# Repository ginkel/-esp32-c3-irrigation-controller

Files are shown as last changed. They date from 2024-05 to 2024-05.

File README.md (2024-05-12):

# ESP32-C3 Plant Watering Controller

A custom PCB for an ESP32-C3 based plant watering controller that features two channels to drive 12V water pumps and one input to check for low water level. If using esphome as [firmware](#firmware) it can be easily integrated into [Home Assistant](https://www.home-assistant.io/).

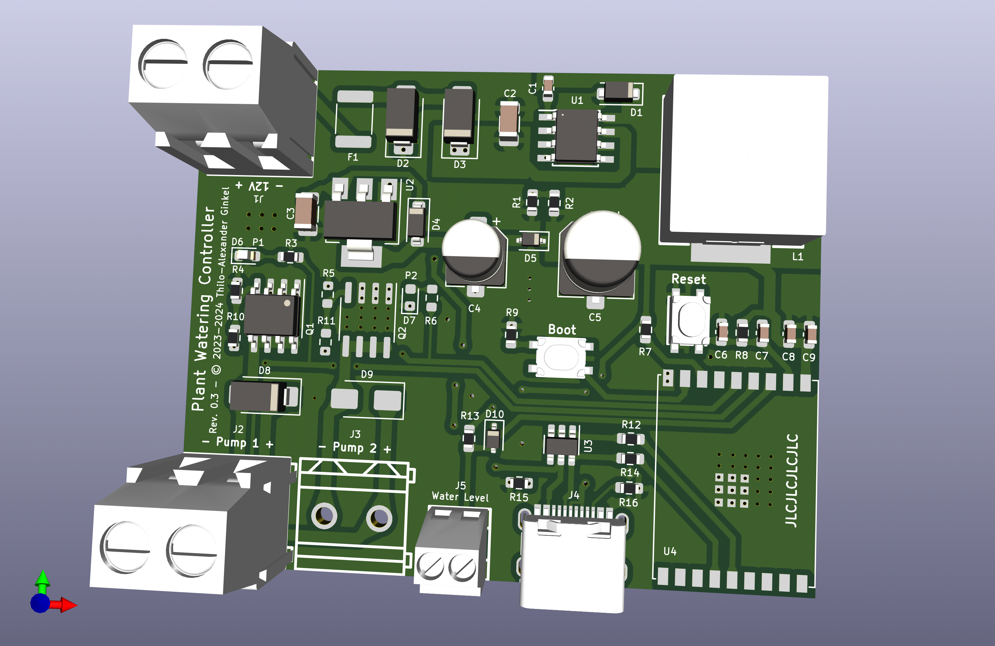
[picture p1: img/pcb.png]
PCB rendering


If you'd like to solder the PCB yourself, the smallest component to be soldered is 0603. The list of components and their placement is available as [interactive BOM](bom/ibom.html).

If you only need one channel (for a single pump), you can leave R5, R6, R11 D7, D9, Q2 and J3 unpopulated.

Documentation is probably far from complete. If you are missing a piece of the puzzle, feel free to open an issue or improve the documentation using a PR.

## Schematic

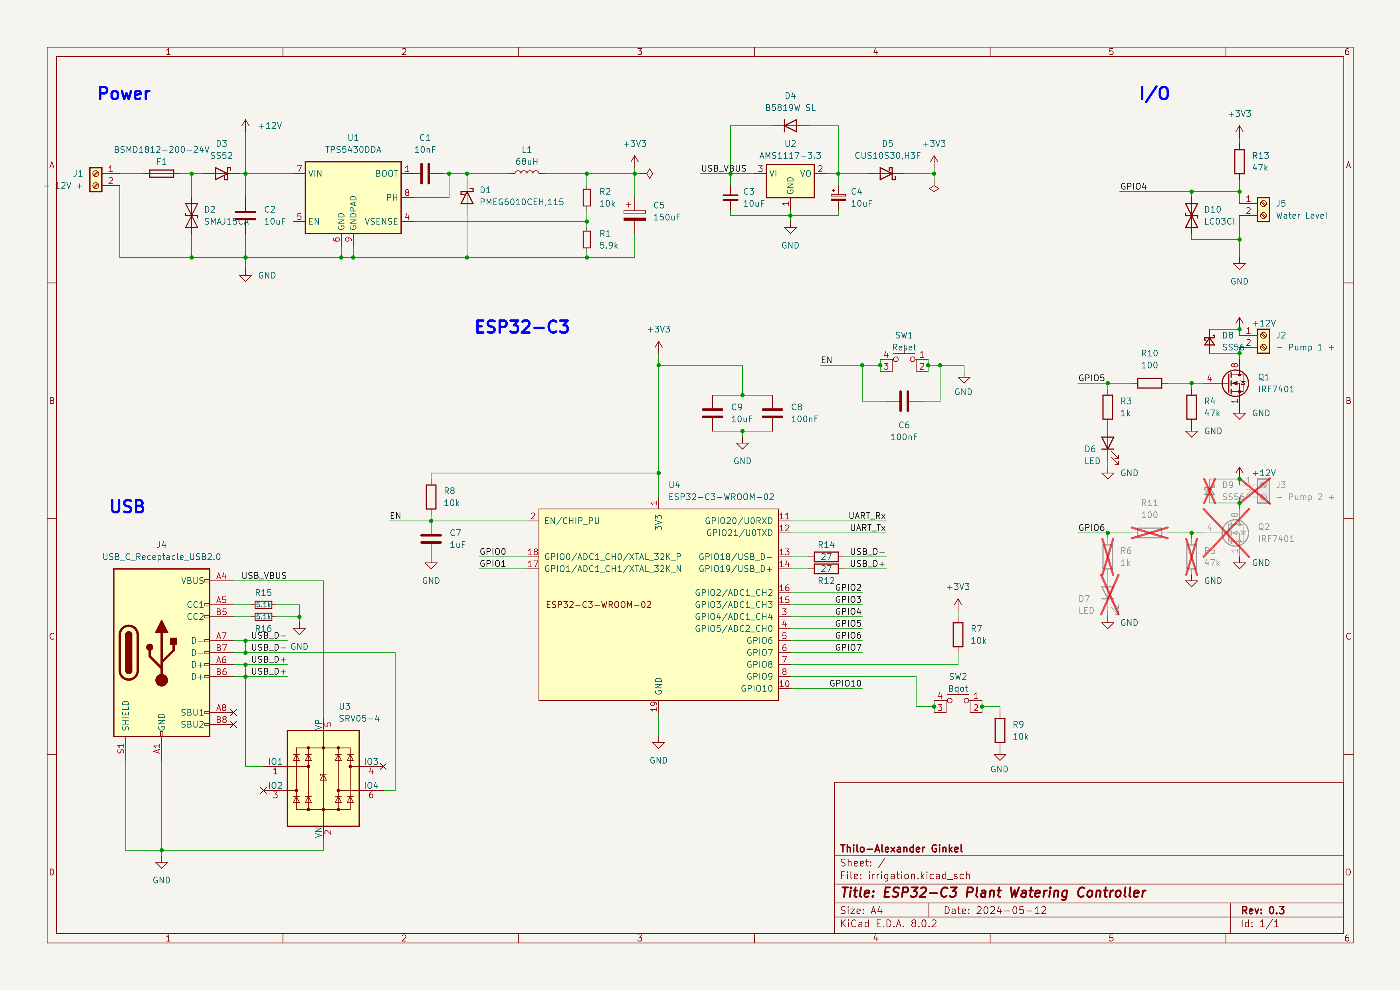
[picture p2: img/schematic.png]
schematics


## BOM

| References | Value | LCSC part # |
|---|---|---|
| C1 | 10nF | C57112 |
| C2 | 10uF | C15849 |
| C3 | 10uF | C89632 |
| C4 | 10uF | C336204 |
| C5 | 150uF | C242120 |
| C6, C8 | 100nF | C1591 |
| C7 | 1uF | C15849 |
| C9 | 10uF | C194427 |
| R2, R7, R8, R9 | 10k | C25804 |
| R3, R6 | 1k | C21190 |
| R4, R5, R13 | 47k | C25819 |
| R10, R11 | 100 | C22775 |
| R12, R14 | 27 | C863706 |
| R15, R16 | 5.1k | C23186 |
| R1 | 5.9k | C23071 |
| L1 | 68uH | C694542 |
| D1 | PMEG6010CEH,115 | C110797 |
| D2 | SMAJ15CA | C110044 |
| D3 | SS52 | C727051 |
| D4 | B5819W SL | C8598 |
| D5 | CUS10S30,H3F | C146335 |
| D6, D7 | LED | C434419 |
| D8, D9 | SS56 | C2904059 |
| D10 | LC03CI | C384865 |
| U1 | TPS5430DDA | C9864 |
| U2 | AMS1117-3.3 | C347222 |
| U3 | SRV05-4 | C85364 |
| U4 | ESP32-C3-WROOM-02 | C2934560 |
| F1 | BSMD1812-200-24V | C206993 |
| SW1, SW2 | XUNPU TS-1089S-02526 | C455282 |
| Q1, Q2 | IRF7401 | C5346818 |
| J1, J2, J3 | DB128L-5.08-2P-GN-P  | C430600 |
| J4 | USB-C Connector | C165948 |
| J5 | DB125-2.54-2P-GN-S | C918120 |

I am sourcing my components from LCSC. If you also do, the LCSC part # may be helpful.

## External Parts

For a full-fledged plant watering solution you'll need some additional components/parts. Links go to AliExpress, but you can of course source the components from other sources if you prefer a different suppliers.

* [Submersible 12V water pump](https://aliexpress.com/item/1005005489175847.html)
* [Water level sensor](https://aliexpress.com/item/1005004306055007.html)
* [Water filter (8mm)](https://aliexpress.com/item/1005005032983727.html)
* [Sprinklers](https://aliexpress.com/item/1005004917374250.html)
* [8mm to 4mm connector](https://aliexpress.com/item/1005004875653640.html)
* 8mm hose
* 4mm hose
* Water reservoir, e.g., IKEA HÅLLBAR (35 l)

## Firmware

The firmware I am running on the controller is based on [esphome](https://esphome.io/). I am using the following snippet (for a single channel and a moisture sensor named `sensor.plant_herbs_balcony_soil_moisture`), which you'll probably want to customize to integrate with your Home Assistant instance and WiFi.

```
globals:
  - id: last_run
    type: time_t
    restore_value: yes
    initial_value: '0'

esphome:
  name: plant-watering
  name_add_mac_suffix: true
  friendly_name: ESP32-C3 Plant Watering Controller
  platformio_options:
    board_build.flash_mode: dio
    board_build.f_flash: 40000000L
    board_build.flash_size: 4MB
    # run with 80 MHz
    board_build.f_cpu: 80000000L

esp32:
  board: esp32-c3-devkitm-1
  framework:
    type: esp-idf
    sdkconfig_options:
      CONFIG_COMPILER_OPTIMIZATION_SIZE: y
  variant: esp32c3

mqtt:
  broker: [...]
  username: [...]
  password: [...]
  on_message:
    - topic: esphome/plant_watering/pump1
      payload: 'ON'
      then:
        - if:
            condition:
              binary_sensor.is_on: water_level
            then:
              - globals.set:
                  id: last_run
                  value: !lambda 'return id(homeassistant_time).now().timestamp;'
              - logger.log: "Turning irrigation 'pump1' on"
              - output.turn_on: pump1
              - logger.log: "Waiting 20s"
              - delay: 20s
              - logger.log: "Turning irrigation 'pump1' off"
              - output.turn_off: pump1
            else:
              - logger.log: "Water level is critical - refusing to turn on irrigation"

output:
  - platform: gpio
    pin:
      number: GPIO5
      mode:
        output: true
        pulldown: true
      drive_strength: 5mA
    id: pump1
  - platform: gpio
    pin:
      number: GPIO6
      mode:
        output: true
        pulldown: true
      drive_strength: 5mA
    id: pump2

binary_sensor:
  - platform: gpio
    pin:
      number: GPIO4
      mode:
        input: true
      inverted: false
    name: "Water Level"
    id: water_level
    filters:
      - delayed_on: 1s
      - delayed_off: 1s
    on_release:
      then:
        - logger.log: "Water level critical - turning off all pumps"
        - output.turn_off: pump1
        - output.turn_off: pump2

sensor:
  - platform: uptime
    name: "ESP32-C3 Plant Watering Controller Uptime"

  - platform: wifi_signal
    name: "ESP32-C3 Plant Watering Controller WiFi Signal"
    update_interval: 15s

  - platform: homeassistant
    name: "Soil humidity"
    entity_id: sensor.plant_herbs_balcony_soil_moisture
    id: plant_herbs_balcony_soil_moisture

text_sensor:
  - platform: template
    name: "ESP32-C3 Plant Watering Controller Last Run"
    icon: mdi:clock-start
    lambda: |-
      return ESPTime::from_epoch_local(id(last_run)).strftime("%Y-%m-%dT%H:%M:%S");
    update_interval: 60s

time:
  - platform: homeassistant
    id: homeassistant_time
    on_time:
      - cron: '00 /5 18-6 * * *'
        then:
        - if:
            condition:
              and:
                - binary_sensor.is_on: water_level
                - lambda: |-
                    return id(plant_herbs_balcony_soil_moisture).state < 55;
                - lambda: |-
                    return id(homeassistant_time).now().is_valid() && (id(homeassistant_time).now().timestamp - id(last_run) > 43200);
            then:
              - globals.set:
                  id: last_run
                  value: !lambda 'return id(homeassistant_time).now().timestamp;'
              - logger.log: "Turning irrigation 'pump1' on"
              - output.turn_on: pump1
              - logger.log: "Waiting 20s"
              - delay: 20s
              - logger.log: "Turning irrigation 'pump1' off"
              - output.turn_off: pump1
            else:
              - logger.log:
                  format: "Water level: %d, average soil moisture: %.1f - refusing to water plants"
                  args: ['id(water_level).state', 'id(weighted_soil_moisture).state']
```

## Integration

The PCB does not offer a built-in mechanism to measure soil humidity, but the [b-parasite](https://github.com/rbaron/b-parasite) open source project provides a suitable DIY capacitive soil moisture sensor that can easily be integrated using ZigBee / Home Assistant.

## Action Shots

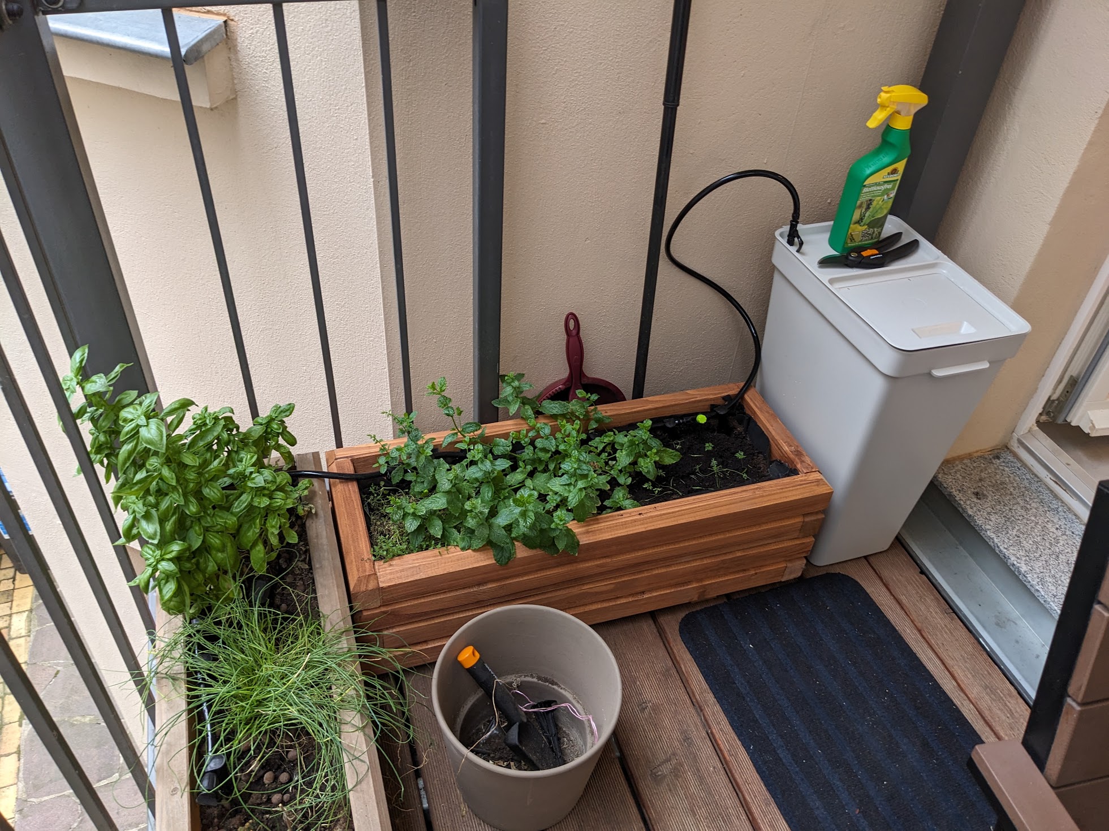
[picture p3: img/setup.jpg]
setup


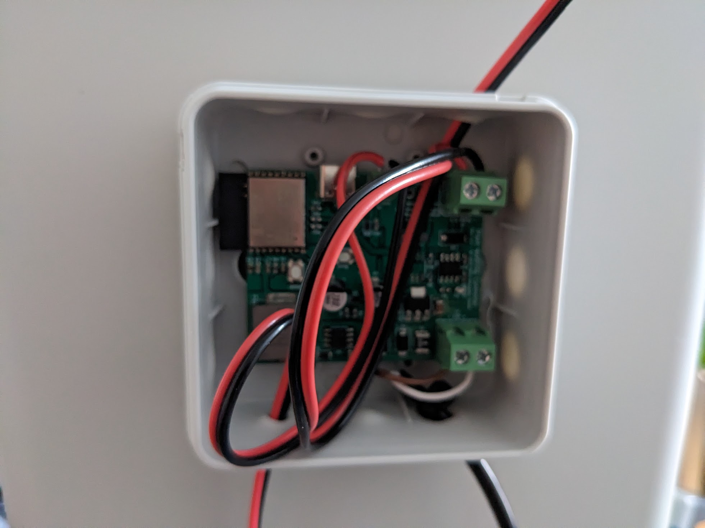
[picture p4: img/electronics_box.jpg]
electronics


## License
The hardware and associated design files are released under the [Creative Commons CC BY-SA 4.0 license](https://creativecommons.org/licenses/by-sa/4.0/).

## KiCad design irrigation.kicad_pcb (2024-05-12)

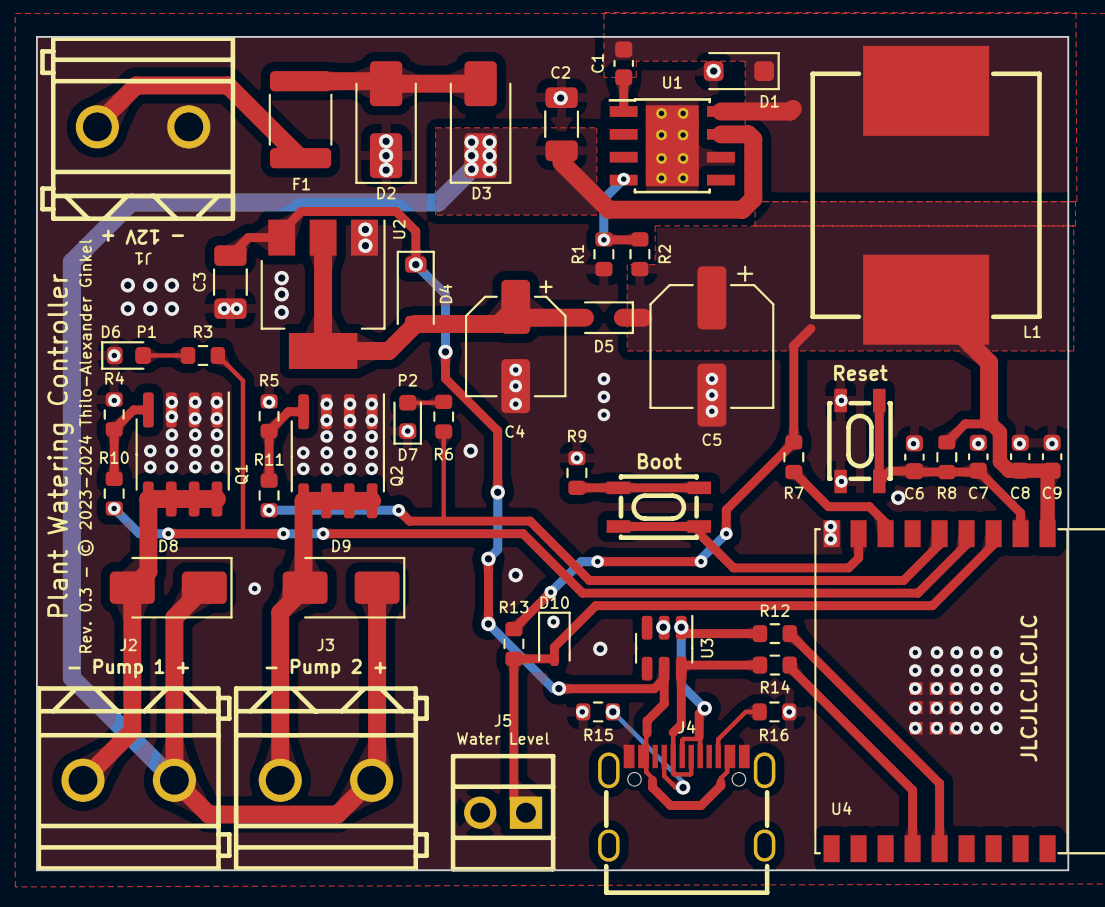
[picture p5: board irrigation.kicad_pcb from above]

Board: 2 copper layers, 57.3 x 46.3 mm, 50 parts (0 on the bottom side), 29 nets.

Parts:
C1: 10nF; C_0603_1608Metric
C2, C3: 10uF; C_1206_3216Metric
C4: 10uF; CP_Elec_5x5.8
C5: 150uF; CP_Elec_6.3x7.7
C6, C8: 100nF; C_0603_1608Metric
C7: 1uF; C_0603_1608Metric
C9: 10uF; C_0603_1608Metric
D1: PMEG6010CEH,115; D_SOD-123F
D2: SMAJ15CA; D_SMA
D3: SS52; D_SMA
D4: B5819W SL; D_SOD-123
D5: CUS10S30,H3F; D_SOD-323
D6, D7: LED; LED_0603_1608Metric
D8, D9: SS56; D_SMA
D10: LC03CI; D_SOD-323
F1: BSMD1812-200-24V; Fuse_1812_4532Metric
J1: - 12V +; CONN-TH_2P-P5.08_DB128L-5.08-2P-GN-P
J2: - Pump 1 +; CONN-TH_2P-P5.08_DB128L-5.08-2P-GN-P
J3: - Pump 2 +; CONN-TH_2P-P5.08_DB128L-5.08-2P-GN-P
J4: USB_C_Receptacle_USB2.0; USB-C_SMD-TYPE-C-31-M-12
J5: Water Level; CONN-TH_DB125-2.54-2P-GN
L1: 68uH; IND-SMD_L12.6-W13.5
Q1, Q2: IRF7401; SOIC-8_3.9x4.9mm_P1.27mm
R1: 5.9k; R_0603_1608Metric
R2, R7, R8, R9: 10k; R_0603_1608Metric
R3, R6: 1k; R_0603_1608Metric
R4, R5, R13: 47k; R_0603_1608Metric
R10, R11: 100; R_0603_1608Metric
R12, R14: 27; R_0603_1608Metric
R15, R16: 5.1k; R_0603_1608Metric
SW1: Reset; SW-SMD_4P-L4.2-W3.3-P2.15-LS5.1
SW2: Boot; SW-SMD_4P-L4.2-W3.3-P2.15-LS5.1
U1: TPS5430DDA; TI_SO-PowerPAD-8_ThermalVias
U2: AMS1117-3.3; SOT-223-3_TabPin2
U3: SRV05-4; SOT-23-6
U4: ESP32-C3-WROOM-02

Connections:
+3V3: C5.1, C8.1, C9.1, D5.1 (K), L1.2, R2.1, R7.1, R8.1, R13.2, U4.1 (3V3)
+12V: C2.1, D3.1 (K), D8.1 (K), D9.1 (K), J2.1, J3.1, U1.7 (VIN)
/EN: C6.2, C7.1, R8.2, SW1.3 (K), SW1.4 (A), U4.2 (EN/CHIP_PU)
/GPIO4: D10.2 (A2), J5.1, R13.1, U4.3 (GPIO4/ADC1_CH4)
/GPIO5: R3.1, R10.1, U4.4 (GPIO5/ADC2_CH0)
/GPIO6: R6.1, R11.1, U4.5 (GPIO6)
/USB_D+: J4.A6 (D+), J4.B6 (D+), R12.2, U3.1 (IO1)
/USB_D-: J4.A7 (D-), J4.B7 (D-), R14.2, U3.6 (IO4)
/USB_VBUS: C3.1, D4.1 (K), J4.A4 (VBUS), J4.A9 (VBUS), J4.B4 (VBUS), J4.B9 (VBUS), U2.3 (VI), U3.5 (VP)
GND: C2.2, C3.2, C4.2, C5.2, C6.1, C7.2, C8.2, C9.2, D1.2 (A), D2.1 (A1), D6.1 (K), D7.1 (K), D10.1 (A1), J1.2, J4.A1 (GND), J4.A12 (GND), J4.B1 (GND), J4.B12 (GND), J5.2, Q1.1 (S), Q1.2 (S), Q1.3 (S), Q2.1 (S), Q2.2 (S), Q2.3 (S), R1.1, R4.2, R5.2, R9.2, R15.2, R16.2, SW1.1, SW1.2, U1.6 (GND), U1.9 (GNDPAD), U2.1 (GND), U3.2 (VN), U4.9 (GND), U4.19 (GND)
unnamed: C1.2, D1.1 (K), L1.1, U1.8 (PH)
unnamed: D2.2 (A2), D3.2 (A), F1.2
unnamed: C4.1, D4.2 (A), D5.2 (A), U2.2 (VO)
unnamed: D6.2 (A), R3.2
unnamed: D7.2 (A), R6.2
unnamed: D8.2 (A), J2.2, Q1.5 (D), Q1.6 (D), Q1.7 (D), Q1.8 (D)
unnamed: D9.2 (A), J3.2, Q2.5 (D), Q2.6 (D), Q2.7 (D), Q2.8 (D)
unnamed: F1.1, J1.1
unnamed: J4.A5 (CC1), R15.1
unnamed: J4.B5 (CC2), R16.1
unnamed: Q1.4 (G), R4.1, R10.2
unnamed: Q2.4 (G), R5.1, R11.2
unnamed: R9.1, SW2.1, SW2.2
unnamed: SW2.3 (K), SW2.4 (A), U4.8 (GPIO9)
unnamed: C1.1, U1.1 (BOOT)
unnamed: R1.2, R2.2, U1.4 (VSENSE)
unnamed: R7.2, U4.7 (GPIO8)
unnamed: R14.1, U4.13 (GPIO18/USB_D-)
unnamed: R12.1, U4.14 (GPIO19/USB_D+)

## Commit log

2023-06-26 Initial import
    [irrigation-B_Cu.gbr, irrigation-B_Mask.gbr, irrigation-B_Paste.gbr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]
2023-06-26 Various bug fixes & improvements
    [irrigation-B_Cu.gbr, irrigation-B_Mask.gbr, irrigation-B_Paste.gbr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]
2023-06-27 Add interactive BOM
    [irrigation.kicad_pcb]
2023-06-27 Cleanup iBOM
    [irrigation.kicad_pcb]
2023-09-05 Downgrade KiCad version
    [irrigation.kicad_pcb, irrigation.kicad_sch]
2024-05-12 Add BOM, fix nets
    [irrigation.kicad_pcb, irrigation.kicad_sch]
2024-05-12 Update PCB & gerber files
    [irrigation-B_Cu.gbr, irrigation-B_Mask.gbr, irrigation-B_Paste.gbr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]

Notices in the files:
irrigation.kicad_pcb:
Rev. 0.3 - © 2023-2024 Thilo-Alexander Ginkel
